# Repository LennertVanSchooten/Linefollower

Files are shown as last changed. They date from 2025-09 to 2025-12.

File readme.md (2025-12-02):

# LineFollower

lege repository die je als template kan gebruiken om een eigen repository te starten voor uw linefollower project

A description of my image


## specifications

microcontroller: Arduino nano (clone)

motors: N20---30:1---500RPM 

h-bridge: DRV8833

sensors: HY-S301

batteries: 2x 18650 lipo

wireless communication: HC-08 

distance sensor - motors: 9.92cm

weight: 214gr

speed: 0.7m/s (voorlopige stabiele snelheid)

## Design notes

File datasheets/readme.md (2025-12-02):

datasheets of the components used in this project

Datasheet van de DRV8833 [drv8833-datasheet.pdf](https://github.com/user-attachments/files/23694670/drv8833-datasheet.pdf)

Datascheet van de Arduino nano [A000005-datasheet.pdf](https://github.com/user-attachments/files/23694715/A000005-datasheet.pdf)

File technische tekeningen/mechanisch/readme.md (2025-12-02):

# ontwerp van het frame



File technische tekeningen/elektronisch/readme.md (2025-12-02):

# PCB ontwerp

a38c5a8e-52b1-4e57-9f7f-d86845e7ee0b

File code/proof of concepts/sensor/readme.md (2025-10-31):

# Sensoren proof of concept

minimale hard- en software die aantoont dat minimaal 6 sensoren onafhankelijk van elkaar kunnen uitgelezen worden (geen calibratie, normalisatie of interpolatie). Hierbij moet een zo groot mogelijk bereik van de AD converter benut worden (indien van toepassing)

**Benodigdheden**  
-	HY-S301
-	Arduino Nano R3

**Stappenplan**
- Sluit de sensor aan de arduino volgens het aansluitschema aan.
- Verbind de arduino met de pc en upload het programma in de arduino.
- test met een wit oppervlak of de waarden veranderen van de sensoren.

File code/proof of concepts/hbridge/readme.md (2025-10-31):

# H-Bridge proof of concept

Welkom in de readme van het H-brug gedeelte van de linefollower.

**Benodigdheden**  
-  DRV8833 microchip
-  Arduino Nano R3
-  	Aslong JGA12-N20-30 DC-Transmissiemotor 6V - 500RPM

**Stappenplan**  
-  De DRV8833 microchip heeft op het breakoutbord 4 ingangen, 4 uitgangen, VCC, GND, EEP & ULT.

-  De ingangen en uitgangen spreken opzich, zeer belangrijk bij de ingangen is dat de pwm's op de zelfde clock snelheid zitten. PWM 3, 5, 6 & 11 hebben een 8bit clocksnelheid. PWM 9 & 10 hebben een 16bit clocksnelheid. ALs 2 soorten clocksnelheden worden gebruikt zullen de motoren een verschillende snelheid hebben.

-  De EEP pin wordt aan de VCC (5V) van de arduino gekoppeld, dit moet zeker verbonden worden anders zal de H-brug niet werken. Als de EEP geen voeding krijgt zal de H-brug in sleep modus staan waardoor de OUT's niet zullen schakelen.

-  De Ult pin wordt met een pull-up weerstand geschakeld, deze dient als fout detectie. Als de H-brug normaal werkt zal deze een hoog signaal hebben waardoor de arduino een laag signaal leest. Als er een interne fout in de H-brug is zal de uitgang laag zijn waardoor de arduino een hoog signaal zal lezen. Dit zullen we a.d.h.v. een HC-05 door sturen naar een gsm.

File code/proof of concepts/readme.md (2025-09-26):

# Proof of Concepts

Een proof of concept is een combinatie van minimale hard- en software om eenvoudig aan te tonen dat iets werkt.  
Proof of concepts kunnen enerzijds als eerste poging dienen om een bepaald onderdeel van het project werkend te krijgen. Anderzijds kunnen ze tijdens het debuggen van het finale project dienen als test om eventuele hardware problemen te elimineren bij onduidelijke problemen.
<br />  
<br />
Een proof of concept bestaat uit
* een elektronisch schema (indien van toepassing)
* minimale code om de voorop gestelde zaken te demonstreren
* minimale uitleg / aandachtspunten
<br />
De elektronische schakelingen van de proof of concepts komen bij voorkeur overeen met deze van de uiteindelijke linefollower, zodat de code zonder aanpassingen op het finale project kan draaien.

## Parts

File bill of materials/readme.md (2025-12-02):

## bill of materials
<br />

|volgnummer|naam|omschrijving|nieuw/recup|kostprijs/stuk (zonder verzendkosten)|aantal|subtotaal|
|---|----|---|---|---|---|---|
| 1| HC-08 Bluetooth module met adapter - clone| bluetooth module | nieuw | €8.50 |  1 |  €8.50 |
| 2| Arduino Nano R3 - kloon - met headers| Arduino Nano | nieuw |  €8.60 |  1 |  €8.60 |
| 3| Female header stackable 6 pin |5x Female headers 6 pin | nieuw |  €2.85 | 0.5 | €1.425 |
| 4| Fasizi 5 x DRV8833|dubbele H-brug | nieuw | €3 | 1 |€3 |
| 5| HY-S301 | 8x IR Lijn Tracking Module | nieuw | €3.50 | 1 | €3.50 |
| 6| Aslong JGA12-N20-30 DC-Transmissiemotor 6V - 500RPM| motor 30:1 | nieuw |  €4.50 | 2 |  €9.00 |
| 7| 15 Pins header Female | fermale headers 15 pinss | nieuw |  €0.31 | 2 | €0.62 |
| 8| 18650 | batterij | nieuw | €1.45 | 2 | €2.90 |
| 9| 2x 18650 Batterijhouder met klemkontacten en losse draden | Batterijhouder |  nieuw | €1.59 | 1 |  €1.59 |
| 10| klemschroefblok 2 pins | | nieuw | €0.55 |2 | €1.10 |
| 11| JLCPCB | zelfontworpen PCB |  nieuw | €4.245 |1 | €4.245 |
| 12| wielen | AliExpress wielen | Nieuw |  €0.98 |  2 |  €1.96 |
| | | | | | | |
| Totaal| | | | | | €46.44 |

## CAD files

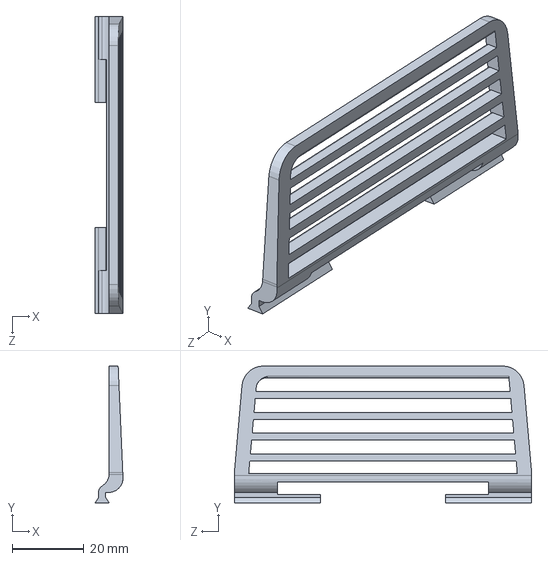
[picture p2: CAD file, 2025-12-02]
technische tekeningen/mechanisch/Spoiler_Lennert.SLDPRT
7.85 x 38.2 x 83.0 mm

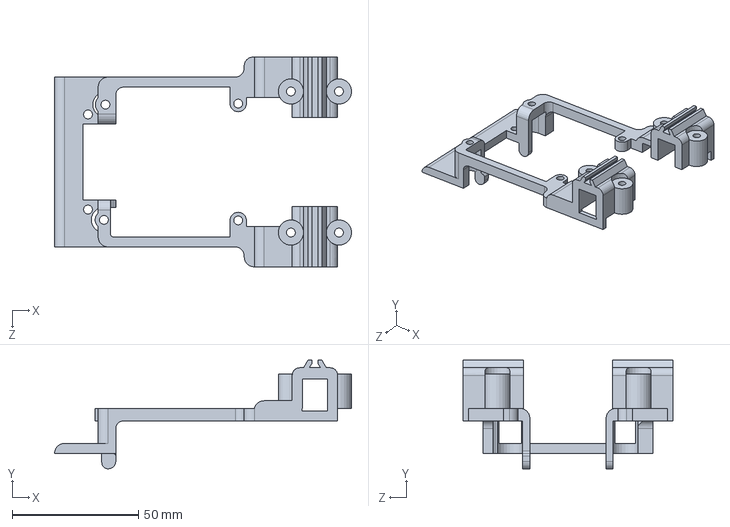
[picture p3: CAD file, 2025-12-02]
technische tekeningen/mechanisch/Frame V9.SLDPRT
117.5 x 43.0 x 83.0 mm

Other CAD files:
technische tekeningen/mechanisch/Frame V9.STL
technische tekeningen/mechanisch/Spoiler_Lennert.STL

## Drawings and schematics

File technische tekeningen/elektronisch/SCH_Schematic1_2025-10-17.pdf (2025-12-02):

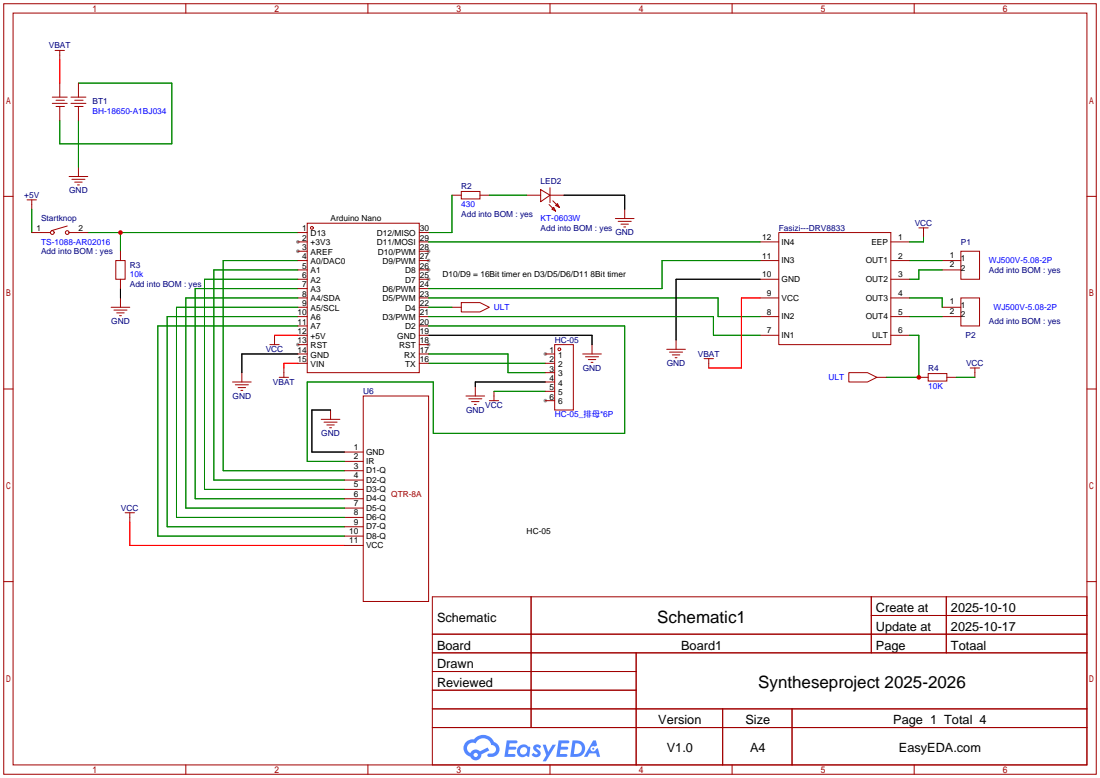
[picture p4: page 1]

Startknop
Add into BOM : yes

Schematic | Schematic1 | Create at | 2025-10-10

Update at | 2025-10-17

Board | Board1 | Page | Totaal
Drawn | | Syntheseproject 2025-2026
Reviewed

Version | Size | Page 1 Total 4
V1.0 | A4 | EasyEDA.com

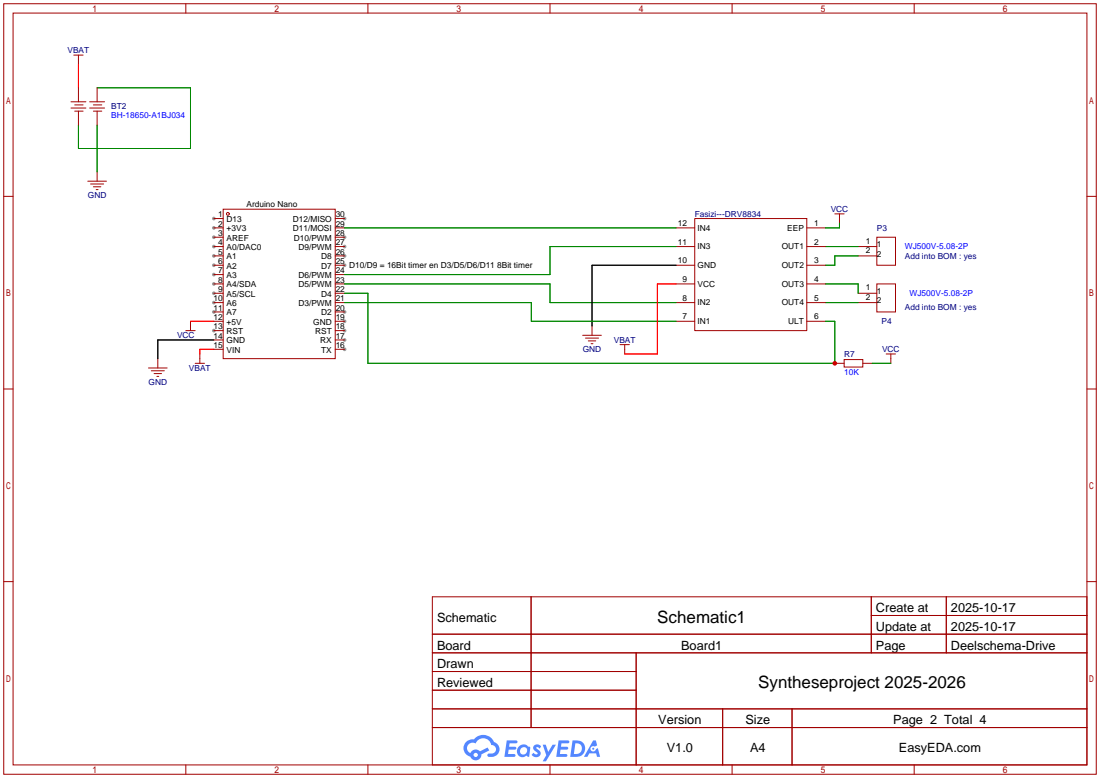
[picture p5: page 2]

Schematic | Schematic1 | Create at | 2025-10-17

Update at | 2025-10-17

Board | Board1 | Page | Deelschema-Drive
Drawn | | Syntheseproject 2025-2026
Reviewed

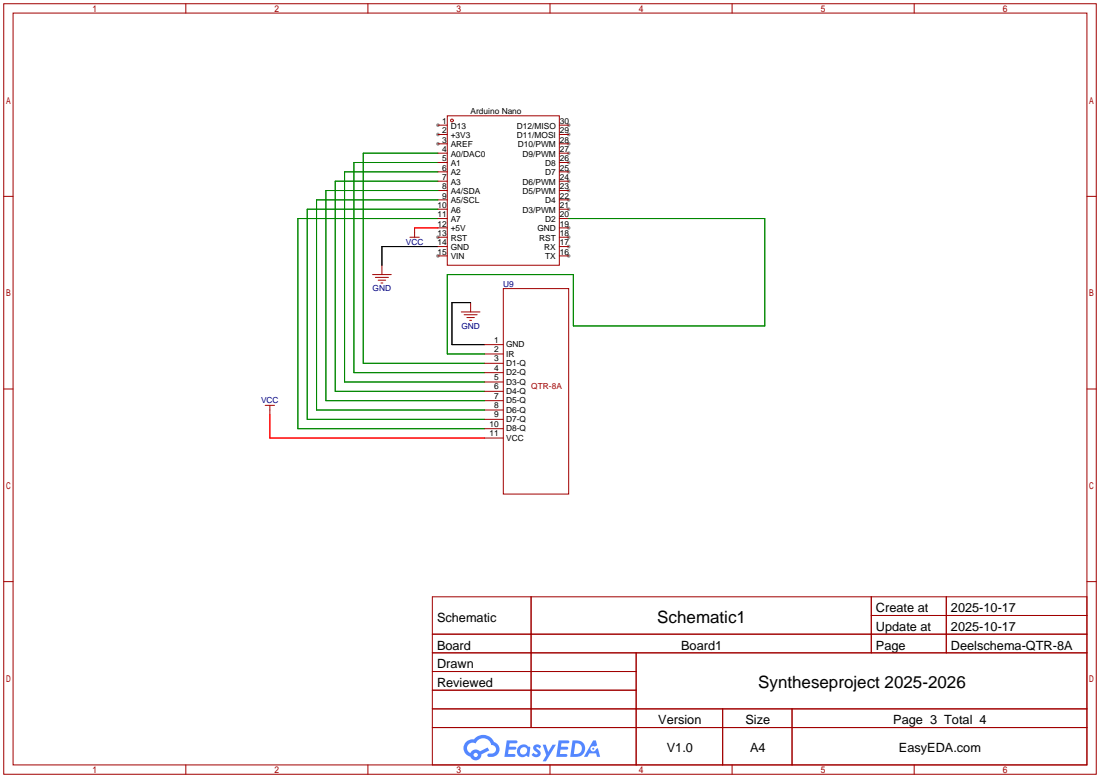
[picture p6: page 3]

Schematic | Schematic1 | Create at | 2025-10-17

Update at | 2025-10-17

Board | Board1 | Page | Deelschema-QTR-8A
Drawn | | Syntheseproject 2025-2026
Reviewed

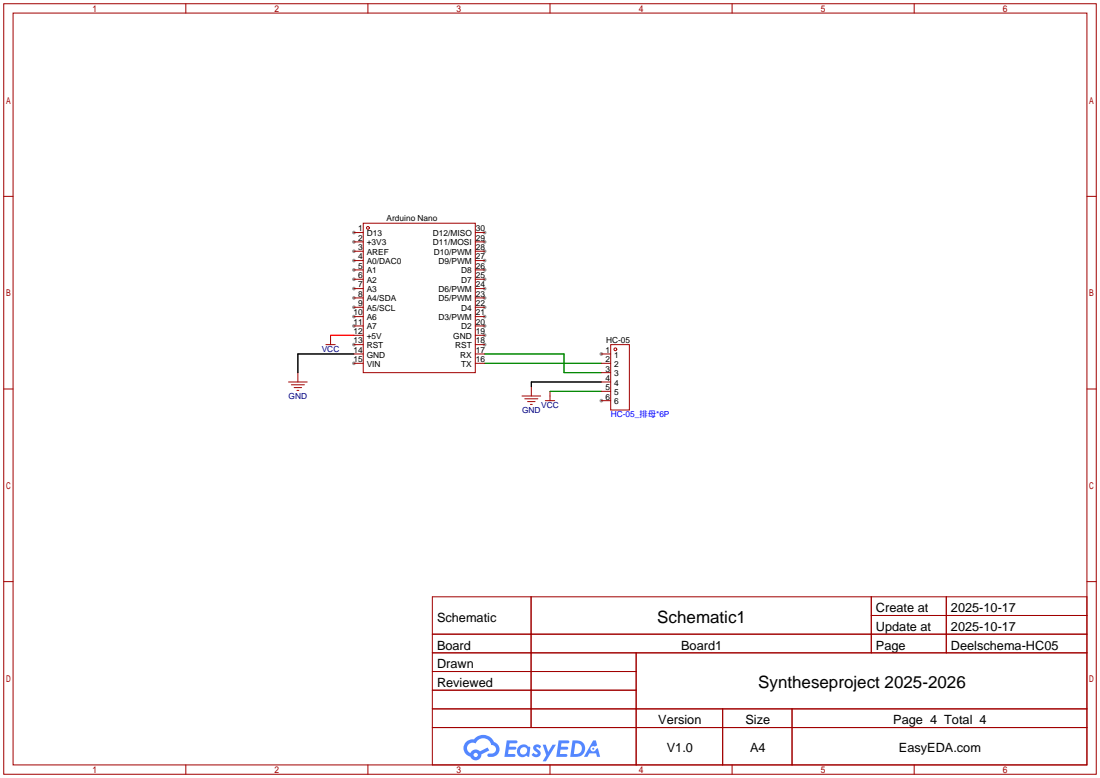
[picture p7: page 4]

Schematic | Schematic1 | Create at | 2025-10-17

Update at | 2025-10-17

Board | Board1 | Page | Deelschema-HC05
Drawn | | Syntheseproject 2025-2026
Reviewed

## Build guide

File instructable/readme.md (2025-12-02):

# Instructable

Een instructable is een stappenplan - zonder verdere uitleg - hoe je vertrekkend van de bill of materials en gebruik makend van de technische tekeningen de robot kan nabouwen. Ook de nodige stappen om de microcontroller te compileren en te uploaden staan beschreven.  

### stap 0
Bestel de componenten uit de BOM, zoveel mogelijk van dezelfde leverancier (tinytronics).

De pcb, onder technische tekeningen -> elektronisch vindt je de elektronische schemas als de pcb file die je kan importeren in easyeada.

De pcb is ontworpen om de weerstanden, drukknop, schakelaar en led er op telaten zetten tijdens productie en is dus mee gerekend in de pcb kosten.
(dit moet je tijdens het bestellen aanduiden want dit wordt niet automatisch gedaan)

### stap 1
test de componenten uit a.d.h.v. de schemas en codes onder de tab code -> proof of concepts. 
deze zullen een goede werking demonstreren van de componenten.

DRV8833 wordt best eerst getest met led's.
Aangeraden om de sensor op een vaste hoogt te monteren om een duidelijk verschil te zien tussen zwart en wit.

### stap 2
Soldeer de female headerds en terminals op de pcb als de draden op de sensor, aangeraden om 0.8mm² stijvedraden te gebruiken (recup van sgg kabel).

### stap 3
Print het frame dat te vinden is onder technische tekeningen -> mechanisch. 
Hier zal je een stl bestand vinden als een solidworks tekening voor als je zelf aanpassingen wilt uitvoeren.
(spoiler stl is ook beschikbaar)

### stap 4
monteer alle componeten op het frame met M3 bouten en moeren. je moet er maar 5 van elk gebruiken (2 voor de sensor, 2 voor de batterijhouder en 1 voor de pcb).

### stap 5
Als de motoren en batterijhouder op het frame zijn bevestigd kan je de draden hiervan solderen.

LET GOED OP!!!!
Batterijhouder: de rode draden van de batterijhouder zullen wij zien als + en zwart als -. We solderen de rode draden op de pcb links van de schakelaar (aan de kant waar VBAT staat) en de zwarte draden rechts van de schakelaar (aan de kant waar GND staat). 
De batterijen zijn via de pcb in serie geschakeld dus we mogen ze extern NIET KRUISEN, ik heb de buitenste batterij aan de buitenste pads gesoldeerd en de batterij aan de binnen kant aan de binnenste pads.

Motoren: de motoren kunnen simpel gesoldeerd worden als ze geklemmed zitten in het frame. hoe dat deze aangesloten worden is de bovenste draden aan de buitenste terminal slots en de onderste aan de binneste slots van hun respectievelijke terminals (links-links & rechts-rechts).

### stap 6 
Upload de basis code dat te vinden is in code->basis. download alle 4 de bestanden en zet deze in dezelfde map. anders zal het programma niet werken.
dit programma bevat een basis werking van het EEPROM geheugen als normalistatie en interpolatie van de sensor en een P regelaar. 

commandes zijn terug tevinden in de gebruikersaanwijzing.

### stap 7
print de parcours. steek de batterijen in de houder (ROOD +, ZWART -) en zet de schakelaar naar binnen toe. 
als alles goed is verlopen zullen nu signalisatie leds van de arduino nano, hc-08 en motordrive branden.

### stap 8
zet de follower op een wit stuk van het parcour en calibreer wit, doe dit ook voor zwart.

Zet intitieel  power= 80, kp= 10 en diff op 0,4.
Nu ben je klaar om te rijden. 
Stuur het commande "run on" and watch the magic happen.

Je zal de instellingen langzaam moeten tweaken want de waarde zullen voor iedereen verschillen.

### stap 9
upload de final code, deze heeft ook een I & D regelaar.
De follower heeft nu de mogelijkheid om de lijn vlotter tevolgen.

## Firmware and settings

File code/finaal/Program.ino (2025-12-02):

#include "SerialCommand.h"
#include "EEPROMAnything.h"

#define SerialPort Serial
#define Baudrate 9600

SerialCommand sCmd(SerialPort);
bool debug;
int status = 0;  // 0 = uit, 1 = aan
unsigned long previous, calculationTime;

const int ledPin = 12;
const int button = 13;
const int sensor[] = { A7, A6, A5, A4, A3, A2, A1, A0 };
bool lastButtonState = LOW;
long normalised[8];
float position;
float debugPosition;
const int M1_IN1 = 5;
const int M1_IN2 = 3;
const int M2_IN3 = 6;
const int M2_IN4 = 11;
float iTerm, lastErr;

struct param_t {
  unsigned long cycleTime;
  int speed;
  int black[8];
  int white[8];
  float diff;
  float kp;
  float ki;
  float kd;
} params;

void setup() {
  ADCSRA &= ~((1<<ADPS2) | (1<<ADPS1) | (1<<ADPS0)); // testen, geeft extra ruis
  ADCSRA |= (1<<ADPS2); // testen, geeft extra ruis // geeft stabiele sensor waarde maar een calc time tijdens run van 792µs
  //ADCSRA = (ADCSRA & 0b11111000) | 0b010; //geeft calc tijd van 712µs maar iets minder stabiele sensor waarden 
  SerialPort.begin(Baudrate);
  pinMode(ledPin, OUTPUT);
  pinMode(button, INPUT);
  pinMode(M1_IN1, OUTPUT);
  pinMode(M1_IN2, OUTPUT);
  pinMode(M2_IN3, OUTPUT);
  pinMode(M2_IN4, OUTPUT);

  sCmd.addCommand("set", onSet);
  sCmd.addCommand("run", onStatus);
  sCmd.addCommand("debug", onDebug);
  sCmd.addCommand("calibrate", onCalibrate);
  sCmd.setDefaultHandler(onUnknownCommand);

  EEPROM_readAnything(0, params);

  SerialPort.println("ready");
}

void loop() {

  Aanzetten();
  sCmd.readSerial();
  unsigned long current = micros();
  if (current - previous >= params.cycleTime)
  {
    previous = current;
    // hier je cyclische code, bv. sensoren uitlezen
    //sensor
    for (int i = 0; i < 8; i++) 
    {
      normalised[i] = map(analogRead(sensor[i]), params.black[i], params.white[i], 0, 1024);
    }
    //interpolatie
    int index = 0;
    for (int i = 1; i < 8; i++) if (normalised[i] < normalised[index]) index = i;

    if (normalised[index] > 500) status = 0;

    //cijfers kunnen veranderen
    if (index == 0) position = -45;
    else if (index == 7) position = 45;
    else {
      int sNul = normalised[index];
      int sMinEen = normalised[index - 1];
      int sPlusEen = normalised[index + 1];

      float b = sPlusEen - sMinEen;
      b = b / 2;

      float a = sPlusEen - b - sNul;

      position = -b / (2 * a);
      position += index;
      //cijfers kunnen veranderen
      position -= 3.5;
      position *= 15;
    }
    debugPosition = position;

    //kp waarde
    float error = -position;
    float output = error * params.kp;

    /*integrerend regelen*/
    iTerm += params.ki*error;
    iTerm = constrain(iTerm, -510, 510);
    output += iTerm;

    /* differentiërend regelen */
    output += params.kd * (error - lastErr);
    lastErr = error;

    output = constrain(output, -510, 510);

    int powerLeft = 0;
    int powerRight = 0;

    //status on
      if (status == 1) if (output >= 0)
      {
        powerLeft = constrain(params.speed + params.diff * output, -255, 255);
        powerRight = constrain(powerLeft - output, -255, 255);
        powerLeft = powerRight + output;
      }
      else 
      {
        powerRight = constrain(params.speed - params.diff * output, -255, 255);
        powerLeft = constrain(powerLeft + output, -255, 255);
        powerRight = powerRight - output;
      }
      analogWrite(M1_IN1, powerLeft > 0 ? powerLeft : 0);
      analogWrite(M1_IN2, powerLeft < 0 ? -powerLeft : 0);
      analogWrite(M2_IN3, powerRight > 0 ? powerRight : 0);
      analogWrite(M2_IN4, powerRight < 0 ? -powerRight : 0);
      }
    if (status == 0) {
      digitalWrite (ledPin,LOW);
    }
  unsigned long difference = micros() - current;
  if (difference > calculationTime) calculationTime = difference;
}

// --- SerialCommand handlers ---
void onUnknownCommand(char* command) {
  SerialPort.print("unknown command: \"");
  SerialPort.print(command);
  SerialPort.println("\"");
}

void onSet() {
  char* param = sCmd.next();
  char* value = sCmd.next();

  if (strcmp(param, "cycle") == 0) params.cycleTime = atol(value);
  else if (strcmp(param, "speed") == 0) params.speed = atol(value);
  else if (strcmp(param, "status") == 0) {
    if (strcasecmp(value, "on") == 0) status = 1;
    else if (strcasecmp(value, "off") == 0) status = 0;
  } else if (strcmp(param, "diff") == 0) params.diff = atof(value);
  else if (strcmp(param, "kp") == 0) params.kp = atof(value);

  if (strcmp(param, "cycle") == 0)
  {
    long newCycleTime = atol(value);
    float ratio = ((float) newCycleTime) / ((float) params.cycleTime);

    params.ki *= ratio;
    params.kd /= ratio;

    params.cycleTime = newCycleTime;
  }
  else if (strcmp(param, "ki") == 0)
  {
    float cycleTimeInSec = ((float) params.cycleTime) / 1000000;
    params.ki = atof(value) * cycleTimeInSec;
  }
  else if (strcmp(param, "kd") == 0)
  {
    float cycleTimeInSec = ((float) params.cycleTime) / 1000000;
    params.kd = atof(value) / cycleTimeInSec;
  }

  EEPROM_writeAnything(0, params);
}

void onCalibrate() {
  char* param = sCmd.next();

  if (strcmp(param, "black") == 0) {
    SerialPort.print("start calibrating black... ");
    for (int i = 0; i < 8; i++) params.black[i] = analogRead(sensor[i]);
    SerialPort.println("done");
  } else if (strcmp(param, "white") == 0) {
    SerialPort.print("start calibrating white... ");
    for (int i = 0; i < 8; i++) params.white[i] = analogRead(sensor[i]);
    SerialPort.println("done");
  }
}

void Aanzetten()
{
  if (status == 0)
  {
    if (digitalRead (button) == 1) 
    {
      iTerm = 0;
     status = 1;
      digitalWrite(ledPin, HIGH);
   }
  }
}

void onStatus()
{
  char* parameter = sCmd.next();
  char* value = sCmd.next();
  if (strcmp(parameter, "on") == 0 )
  {
    iTerm = 0;
   status = 1;
   digitalWrite (ledPin,HIGH);
  }
  else if (strcmp(parameter, "off") == 0 )
  {
   status = 0;
   digitalWrite (ledPin,HIGH);
  }
}

void onDebug() {
  SerialPort.print("cycle time: ");
  SerialPort.println(params.cycleTime);

  SerialPort.print("black: ");
  for (int i = 0; i < 8; i++) {
    SerialPort.print(params.black[i]);
    SerialPort.print(" ");
  }
  SerialPort.println(" ");

  SerialPort.print("white: ");
  for (int i = 0; i < 8; i++) {
    SerialPort.print(params.white[i]);
    SerialPort.print(" ");
  }
  SerialPort.println(" ");

  SerialPort.print("normalised: ");
  for (int i = 0; i < 8; i++) {
    SerialPort.print(normalised[i]);
    SerialPort.print(" ");
  }
  SerialPort.println(" ");

  SerialPort.print("position: ");
  SerialPort.println(debugPosition);

  SerialPort.print("speed: ");
  SerialPort.println(params.speed);

  SerialPort.print("status: ");
  SerialPort.println(status);

  SerialPort.print("diff: ");
  SerialPort.println(params.diff);

  SerialPort.print("kp: ");
  SerialPort.println(params.kp);

  float cycleTimeInSec = ((float) params.cycleTime) / 1000000;
  float ki = params.ki / cycleTimeInSec;
  SerialPort.print("Ki: ");
  SerialPort.println(ki);

  float kd = params.kd * cycleTimeInSec;
  SerialPort.print("Kd: ");
  SerialPort.println(kd);

  SerialPort.print("calculation time: ");
  SerialPort.println(calculationTime);
  calculationTime = 0;
}

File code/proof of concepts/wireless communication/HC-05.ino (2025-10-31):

#include <SoftwareSerial.h>

SoftwareSerial BTserial(10, 11); // TX, RX van de HC-05
const int led1Pin = 9;           // LED 1 (ON/OFF)
const int led2Pin = 6;          // LED 2 (PWM)

int led2Value = 128;    // Basiswaarde voor LED2 (0-255)

void setup() {
  pinMode(led1Pin, OUTPUT);
  pinMode(led2Pin, OUTPUT);

  Serial.begin(9600);
  BTserial.begin(9600);

  Serial.println("Bluetooth Dual LED control ready.");
}

void loop() {
  analogWrite(led2Pin, led2Value);
  if (BTserial.available()) {
    String command = BTserial.readStringUntil('\n');
    command.trim();

    if (command.equalsIgnoreCase("ON")){
      digitalWrite(led1Pin, HIGH);
    }

    if (command.equalsIgnoreCase("OFF")){
      digitalWrite(led1Pin, LOW);
    }

    if (command.startsWith("PWM")) {
      int val = command.substring(4).toInt();
      val = constrain(val, 0, 255);
      led2Value = val; // sla waarde op zodat hij behouden blijft
    }
  }
}
